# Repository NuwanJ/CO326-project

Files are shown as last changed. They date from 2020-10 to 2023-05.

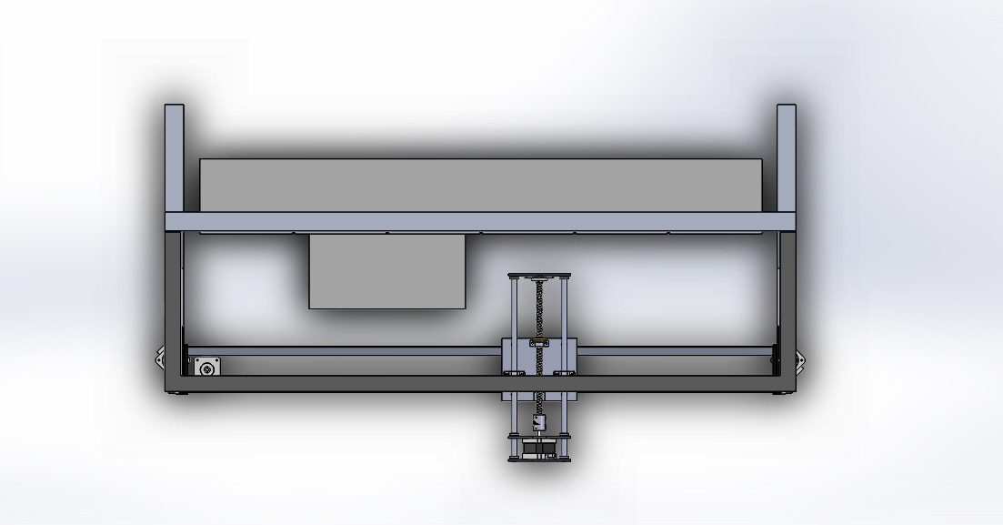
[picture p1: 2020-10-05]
views/top.JPG

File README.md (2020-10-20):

# CNC base 3-axis remotely controlled pick and place robot
### CO326 Computer Systems Engineering

## Overview
Overview
Over the past few decades technology has been evolving rapidly in so many aspects and fields to reach out to the human population in a more user-friendly manner. With these technological developments, new terms like “distance learning”, “remote laboratories”, “virtual learning environments” etc have emerged. However, labs have the greatest potential to overcome the bottleneck in distance education. The goal of Remote Laboratory implementation is to grant students access to laboratory equipment and cover physical laboratory exercises remotely.

A programmable logic controller (PLC) is a special purpose industrial computer/controller that has been adapted to control manufacturing processes. Hence, PLC is widely used in manufacturing to organize complex tasks like security monitoring, automatic control production lines, and management of energy consumption. As a result, there is a great need for engineers with knowledge of PLC. High cost, limited equipment, and limited access to this equipment make it difficult to access everyone.

Hence, connecting PLC with the remote laboratory enables educational institutions to offer programs to a much broader target group of potential students who under no circumstances are able to travel to and attend on-site sessions.

In this project, we hope to develop a CNC (Computer Numerical Control) based pick and place arm, which will help to try different wiring arrangements in a PLC rig and try experiments one it remotely.

Figure 1: An example of a Pick and Place CNC machine

Figure 2: PLC Test Rig of the department of computer engineering

## Specifications
### Software Layer
Web HMI with Javascript
MQTT broker for communication
### Hardware Software Interface
Using standard G-code language for machine control
A firmware like Merlin/Gerber will be supposed to use
Communication is done by USART protocol, with a baud rate of 115000bps
### Hardware Layer
- Nema17 standard stepper motors for motion control
- DRV8825 for stepper motor control
- Arduino Mega 2560 for motion planning

# Methodology

It is constructed using the CNC technology, using Stepper motors with a combination of Screw and Bolt mechanism (for Y and Z axises) and Belt and Pulley mechanism (For X axis). Stepper motors are driven by DRV8825 Step stick drivers with microstepping of 1/16 mode. The microcontroller for the machine is Arduino Mega 2560, with the support of RAMPS 1.4 shield for additional hardware.

The firmware we used is known as GRBL, a well known firmware which drives CNC machines using AVR family microcontrollers. We used GCODE to instruct the machine about movements in 3d space. The software named ‘Candle’ is used to control the machine from PC, and send machine commands as well as configuration commands.    

Communication protocol between HMI and the server needed careful consideration. The messages should be exchanged through the public internet and it should be lightweight since the messages need to arrive with minimum latency which could potentially disrupt the operation of the CNC machine. Therefore, the protocol should be able to handle unreliable networks. Also the messages only contain small commands that need to be passed to the hardware controller. Therefore, the message overhead should be minimum. And most importantly it should be able to handle multiple users. So students can work in groups controlling the PLC rig remotely. Considering all these requirements we used MQTT (Message Queue Telemetry Transport) as the message passing protocol. Because, MQTT is a lightweight message protocol that is based on a subscription-publishing model, in which publishers send messages to a server and this is who forwards messages to subscribers avoiding point-to-point connections between subscribers and publishers.

Students can log into the remote platform using the HMI developed using Javascript (along with HTML and CSS). Then they can use the HMI to send signals to control the CNC machine. The control messages get published to a MQTT broker. A server physically connected to the hardware controller subscribed to the MQTT broker receives the control messages. The control messages contain GCODE commands needed to control  the machine. The server sends the G-CODE commands through a serial interface to the ATMEGA 2560 which runs the GRBL. GRBL converts the control signals to electronic signals and sends to the motor driver, which controls the three server motors. This moves the 3-axis of the CNC machine.   

## Design





### Team Members
 - Jaliyagoda A.J.N.M. (E/15/140)
 - Karunarathna S.D.D.D. (E/15/173)
 - Tennakoon T.M.P.B. (E/15/350)

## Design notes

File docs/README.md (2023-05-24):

---
layout: home
permalink: index.html

# Please update this with your repository name and title
repository-name: e15-co326-remotely-controlled-cnc-robot
title: CNC base 3-axis remotely controlled pick and place robot
---

# CNC base 3-axis remotely controlled pick and place robot

---

## Team
- Jaliyagoda A.J.N.M. (E/15/140)
- Karunarathna S.D.D.D. (E/15/173)
- Tennakoon T.M.P.B. (E/15/350)

## Table of Contents
1. [Introduction](#introduction)
2. [Specifications](#specifications)
3. [Methodology](#methodology)
4. [Design](#design)
5. [Links](#links)

---

# Introduction
Over the past few decades technology has been evolving rapidly in so many aspects and fields to reach out to the human population in a more user-friendly manner. With these technological developments, new terms like “distance learning”, “remote laboratories”, “virtual learning environments” etc have emerged. However, labs have the greatest potential to overcome the bottleneck in distance education. The goal of Remote Laboratory implementation is to grant students access to laboratory equipment and cover physical laboratory exercises remotely.

A programmable logic controller (PLC) is a special purpose industrial computer/controller that has been adapted to control manufacturing processes. Hence, PLC is widely used in manufacturing to organize complex tasks like security monitoring, automatic control production lines, and management of energy consumption. As a result, there is a great need for engineers with knowledge of PLC. High cost, limited equipment, and limited access to this equipment make it difficult to access everyone.

Hence, connecting PLC with the remote laboratory enables educational institutions to offer programs to a much broader target group of potential students who under no circumstances are able to travel to and attend on-site sessions.

In this project, we hope to develop a CNC (Computer Numerical Control) based pick and place arm, which will help to try different wiring arrangements in a PLC rig and try experiments one it remotely.

Figure 1: An example of a Pick and Place CNC machine

Figure 2: PLC Test Rig of the department of computer engineering

## Specifications

### Software Layer
Web HMI with Javascript
MQTT broker for communication

### Hardware Software Interface
Using standard G-code language for machine control
A firmware like Merlin/Gerber will be supposed to use
Communication is done by USART protocol, with a baud rate of 115000bps

### Hardware Layer
- Nema17 standard stepper motors for motion control
- DRV8825 for stepper motor control
- Arduino Mega 2560 for motion planning

# Methodology

It is constructed using the CNC technology, using Stepper motors with a combination of Screw and Bolt mechanism (for Y and Z axises) and Belt and Pulley mechanism (For X axis). Stepper motors are driven by DRV8825 Step stick drivers with microstepping of 1/16 mode. The microcontroller for the machine is Arduino Mega 2560, with the support of RAMPS 1.4 shield for additional hardware.

The firmware we used is known as GRBL, a well known firmware which drives CNC machines using AVR family microcontrollers. We used GCODE to instruct the machine about movements in 3d space. The software named ‘Candle’ is used to control the machine from PC, and send machine commands as well as configuration commands.    

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

Students can log into the remote platform using the HMI developed using JavaScript (along with HTML and CSS). Then they can use the HMI to send signals to control the CNC machine. The control messages get published to a MQTT broker. A server physically connected to the hardware controller subscribed to the MQTT broker receives the control messages. The control messages contain GCODE commands needed to control  the machine. The server sends the G-CODE commands through a serial interface to the ATMEGA 2560 which runs the GRBL. GRBL converts the control signals to electronic signals and sends to the motor driver, which controls the three server motors. This moves the 3-axis of the CNC machine.   

## Design





## Funding

This project was funded by the *Prof. Suhada Jayasuriya Project Support Fund* through *PEFAA* [https://pefaa.net/](https://pefaa.net/).
PEFAA

## Links

- [Project Repository](https://github.com/cepdnaclk/{{ page.repository-name }}){:target="_blank"}
- [Project Page](https://cepdnaclk.github.io/{{ page.repository-name}}){:target="_blank"}
- [Department of Computer Engineering](http://www.ce.pdn.ac.lk/)
- [University of Peradeniya](https://eng.pdn.ac.lk/)

[//]: # (Please refer this to learn more about Markdown syntax)
[//]: # (https://github.com/adam-p/markdown-here/wiki/Markdown-Cheatsheet)

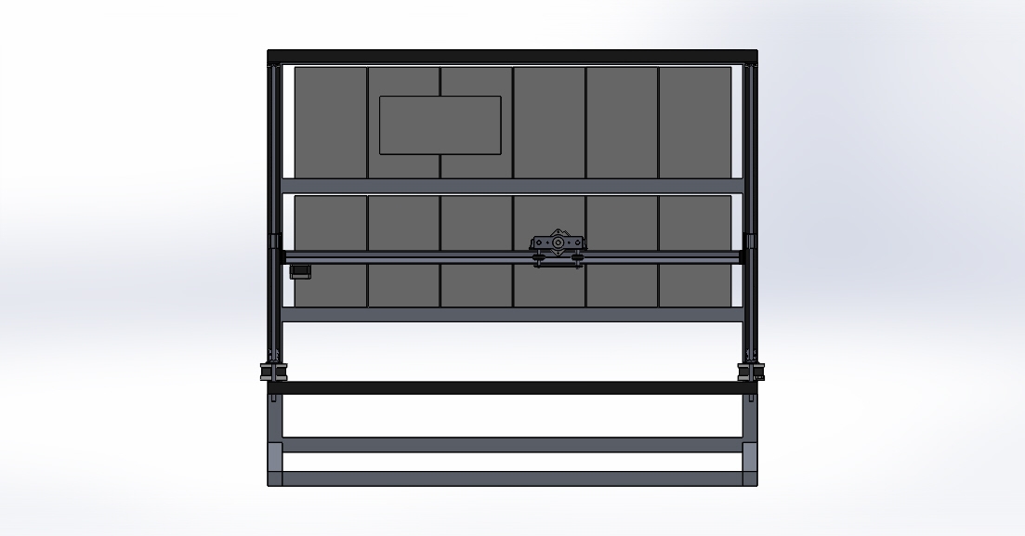
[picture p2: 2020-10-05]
views/front.JPG

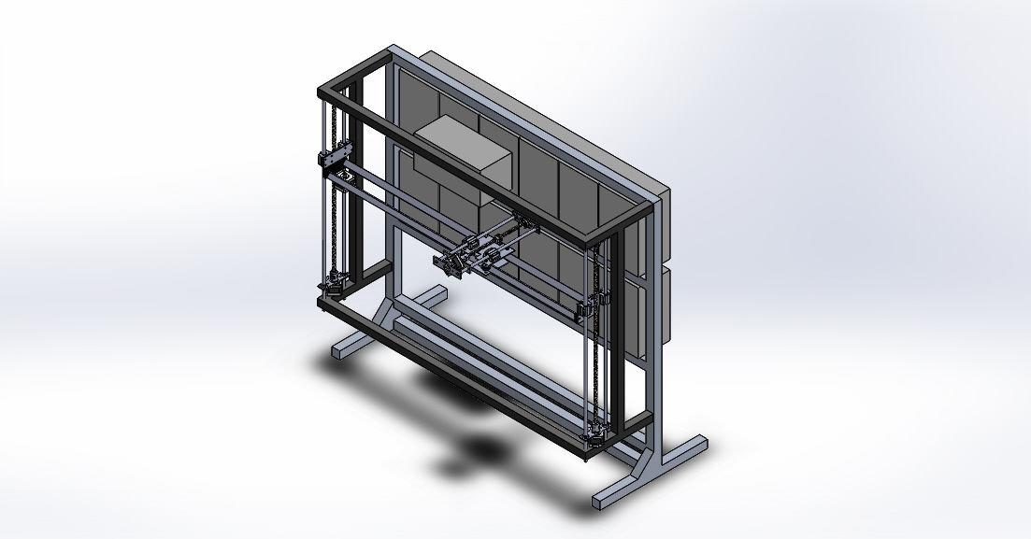
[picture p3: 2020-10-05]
views/orthogonal.JPG

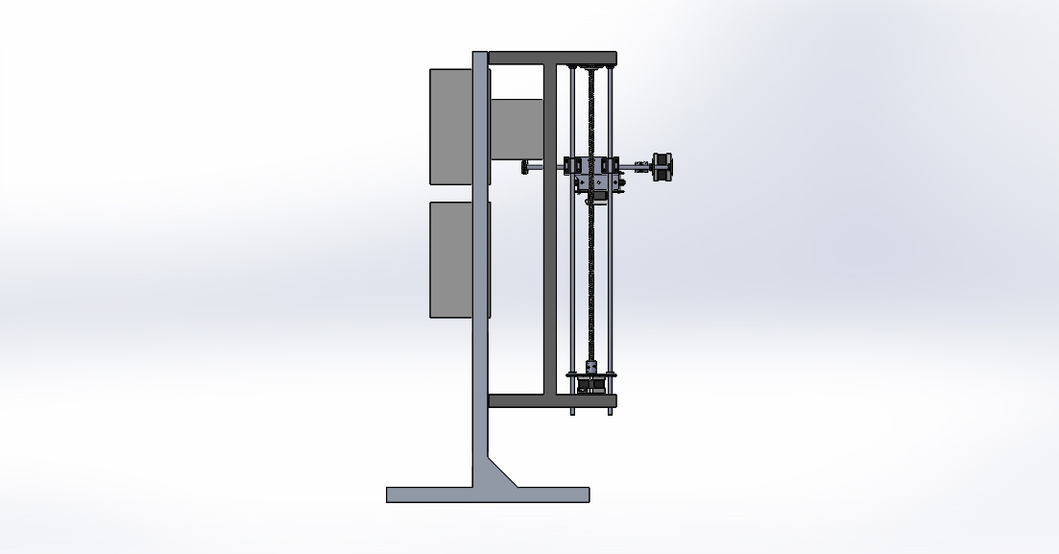
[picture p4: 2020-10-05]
views/side.JPG

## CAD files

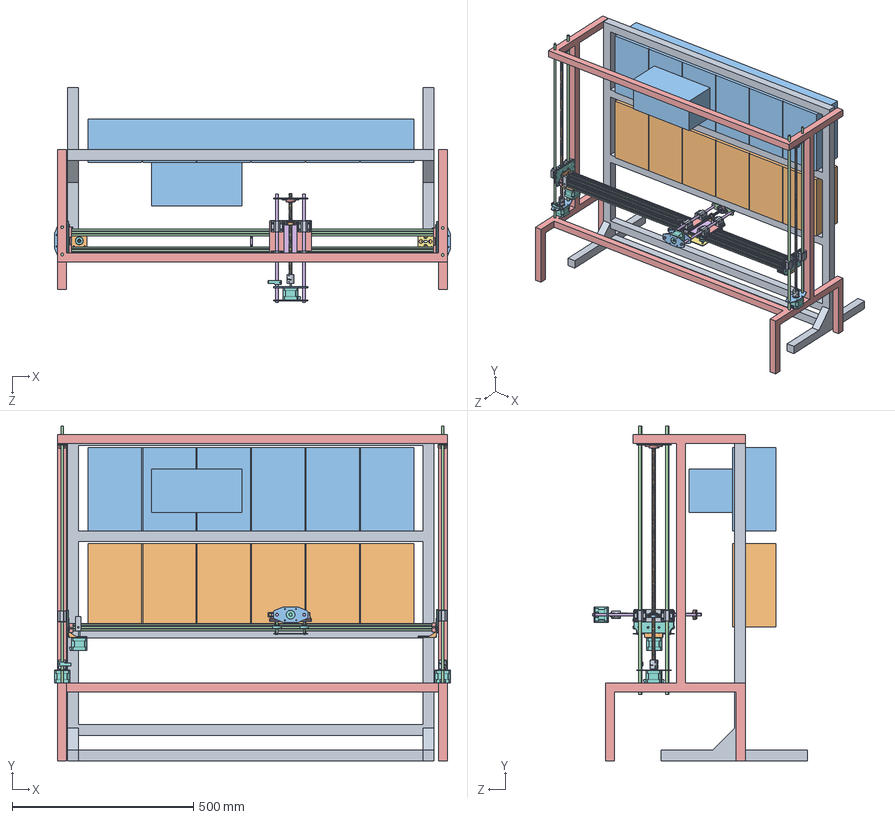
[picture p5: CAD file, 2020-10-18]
CAD/assembly.SLDASM
1092.1 x 923.0 x 593.6 mm
base_frame
components_lower
components_upper
8x600_SmoothRod x 4
kf8_kf08KFL08 x 3
kf8_kf08608RS x 3
kf8_kf08MOSCAM2,5 x 6
nema-17 x 4
5x8_shaft_coupling x 3
Trapezoidal lead screw tr8x8-4 x 2
axis_bracketA x 5
axis_bracketB x 3
metal_frame
x_bearing_bracket_top x 2
x_bearing_bracket_bottom
pom_wheel x 4
SC8UU x 8
T8_bracket
t8-nut x 3
M8x40 x 4
z_bearing_spacer x 4
z_smooth_rod x 2
z_lead_screw
y_bearing_bracket x 4
y_bearing_bracket_b x 2
Nema17_bracket x 2
T8_bracket_b x 2
2020_V-Slot x 2
2020_holder x 2
2020_spacer
pulley_idler_holder
y_limit_switch_holder x 2
x_limit_switch_holder

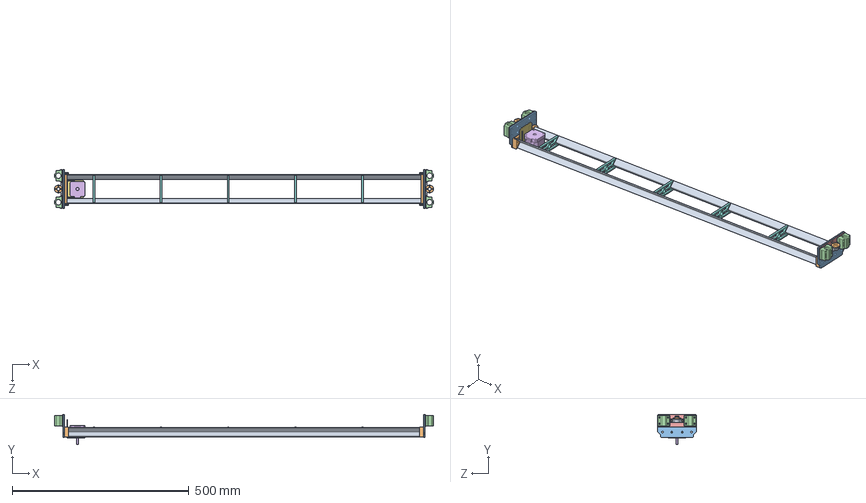
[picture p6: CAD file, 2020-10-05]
CAD/SubAssembly/x-assembly.SLDASM
1072.0 x 85.3 x 109.0 mm
x_rail x 2
x_rail_spacer_end x 2
y_bearing_bracket x 4
SC8UU x 4
y_bearing_bracket_b x 2
nema-17
Nema17_bracket
x_rail_spacer_mid x 5
T8_bracket_b x 2
t8-nut x 2

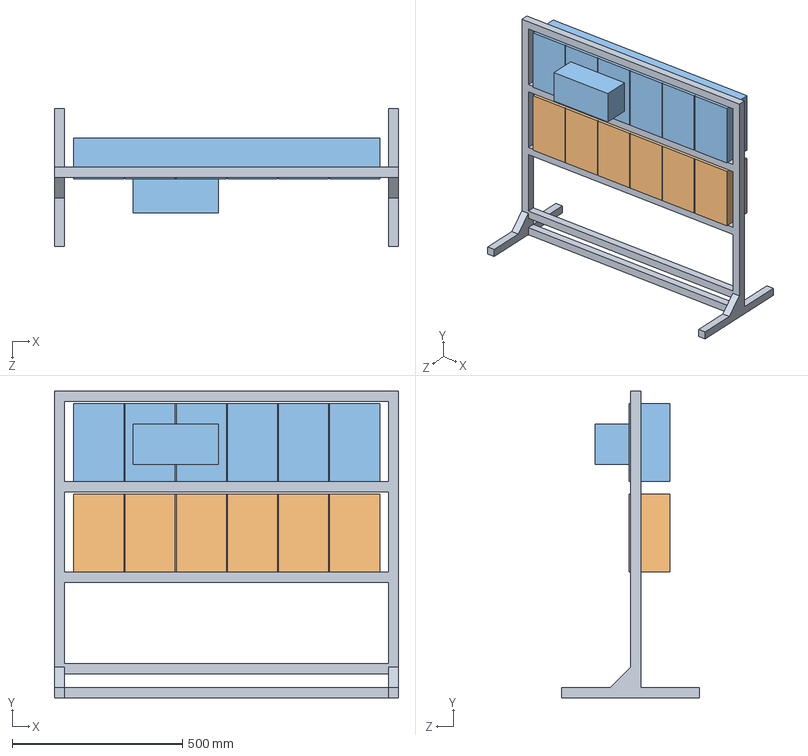
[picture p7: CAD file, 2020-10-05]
CAD/plc_rig.SLDASM
1010.0 x 900.0 x 405.0 mm
base_frame
components_lower
components_upper

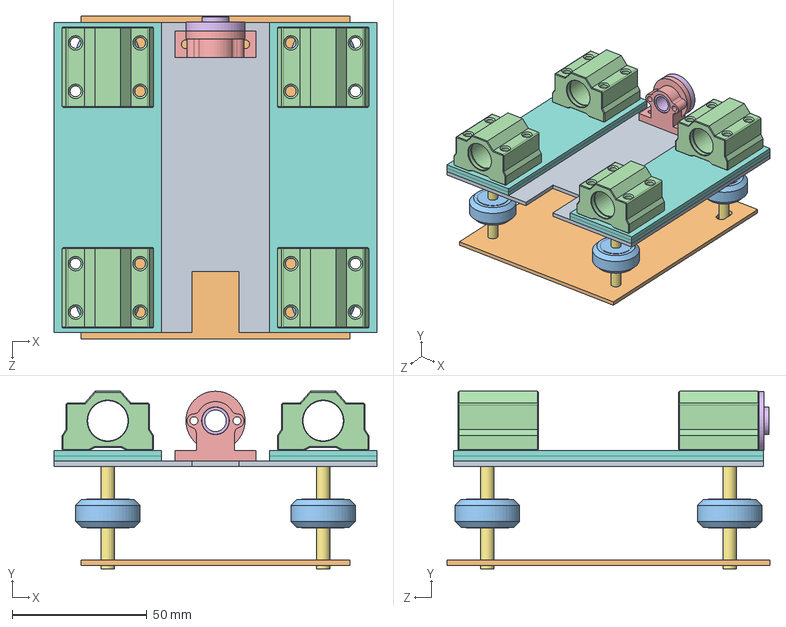
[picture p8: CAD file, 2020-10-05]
CAD/SubAssembly/z-assembly.SLDASM
120.0 x 66.0 x 120.0 mm
x_bearing_bracket_top
x_bearing_bracket_bottom
pom_wheel x 4
SC8UU x 4
T8_bracket
t8-nut
M8x40 x 4
z_bearing_spacer x 4

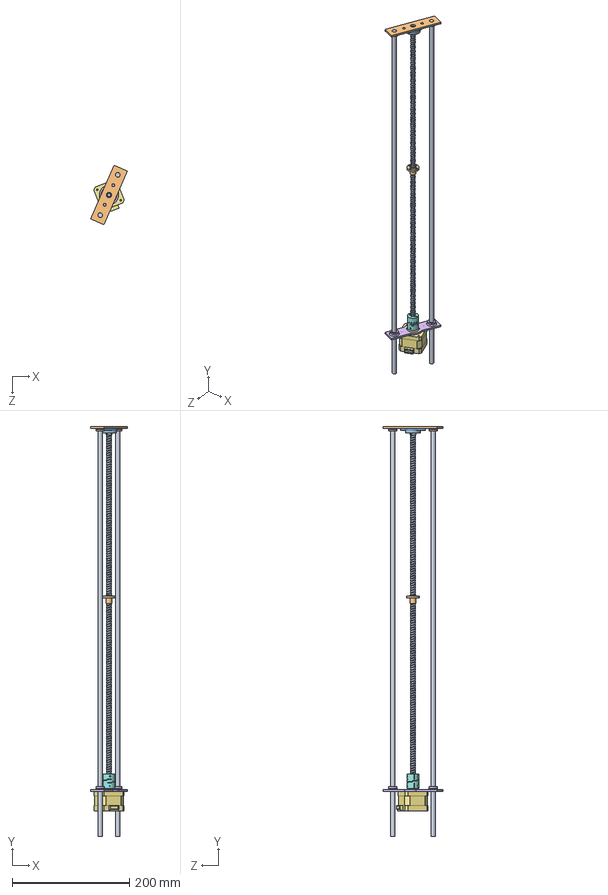
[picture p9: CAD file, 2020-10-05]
CAD/SubAssembly/y-assembly.SLDASM
63.0 x 700.0 x 101.6 mm
8x600_SmoothRod x 2
Y_linear_bracket
kf8_kf08KFL08
kf8_kf08608RS
kf8_kf08MOSCAM2,5 x 2
Y_linear_bracket_withMotor
nema-17
5x8_shaft_coupling
Trapezoidal lead screw tr8x8-4
t8-nut

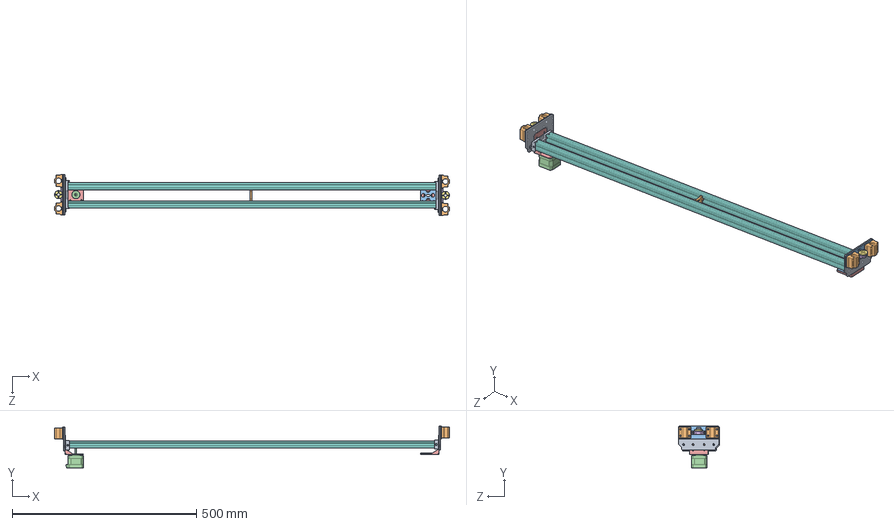
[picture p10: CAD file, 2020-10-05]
CAD/SubAssembly/x-assembly_v2.SLDASM
1071.5 x 113.4 x 110.8 mm
y_bearing_bracket x 4
SC8UU x 4
y_bearing_bracket_b x 2
nema-17
Nema17_bracket x 2
T8_bracket_b x 2
t8-nut x 2
2020_V-Slot x 2
2020_holder x 2
2020_spacer
pulley_idler_holder

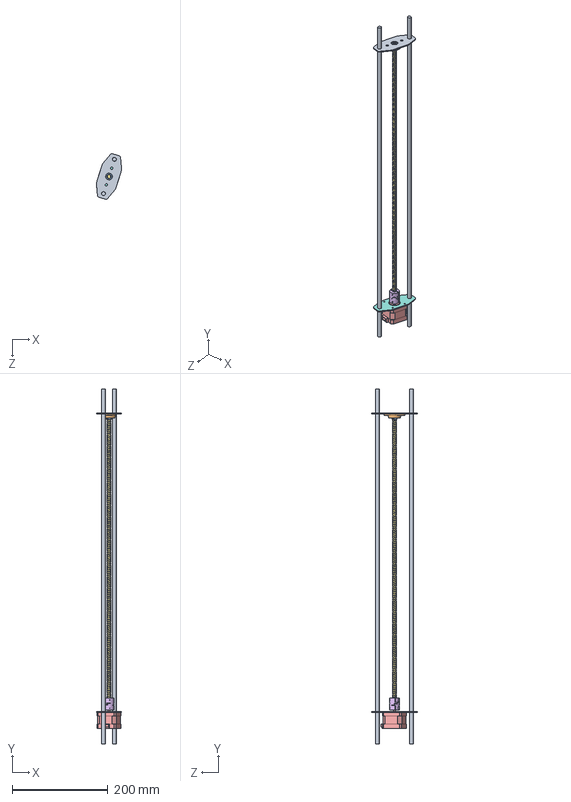
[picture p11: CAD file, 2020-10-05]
CAD/y-assembly.SLDASM
52.8 x 740.0 x 95.3 mm
8x600_SmoothRod x 2
kf8_kf08KFL08
kf8_kf08608RS
kf8_kf08MOSCAM2,5 x 2
nema-17
5x8_shaft_coupling
Trapezoidal lead screw tr8x8-4
axis_bracketA
axis_bracketB

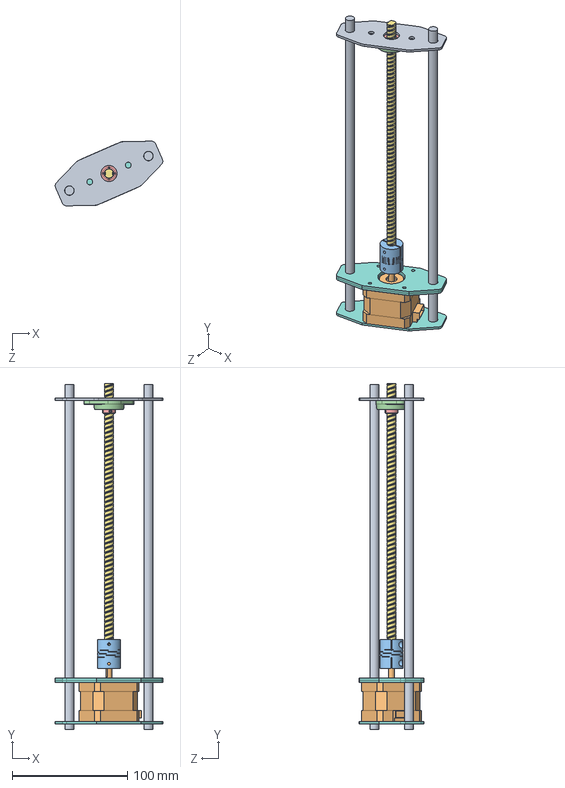
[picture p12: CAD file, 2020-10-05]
CAD/SubAssembly/z-moving-arm.SLDASM
93.6 x 300.7 x 56.3 mm
z_smooth_rod x 2
nema-17
5x8_shaft_coupling
kf8_kf08KFL08
kf8_kf08608RS
kf8_kf08MOSCAM2,5 x 2
z_lead_screw
axis_bracketA x 3
axis_bracketB

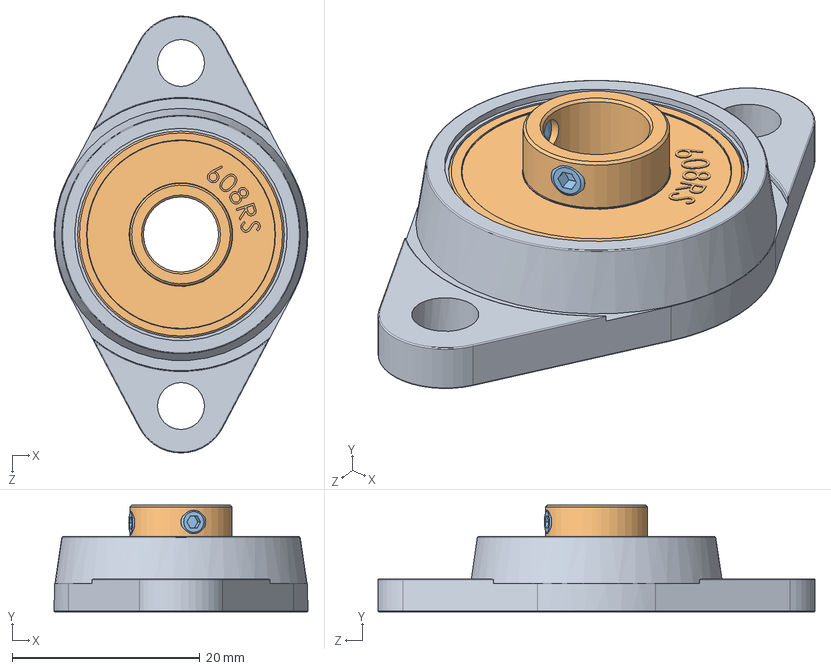
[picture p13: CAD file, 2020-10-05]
CAD/StdParts/KFL08.SLDASM
27.0 x 11.4 x 46.5 mm
kf8_kf08KFL08
kf8_kf08608RS
kf8_kf08MOSCAM2,5 x 2

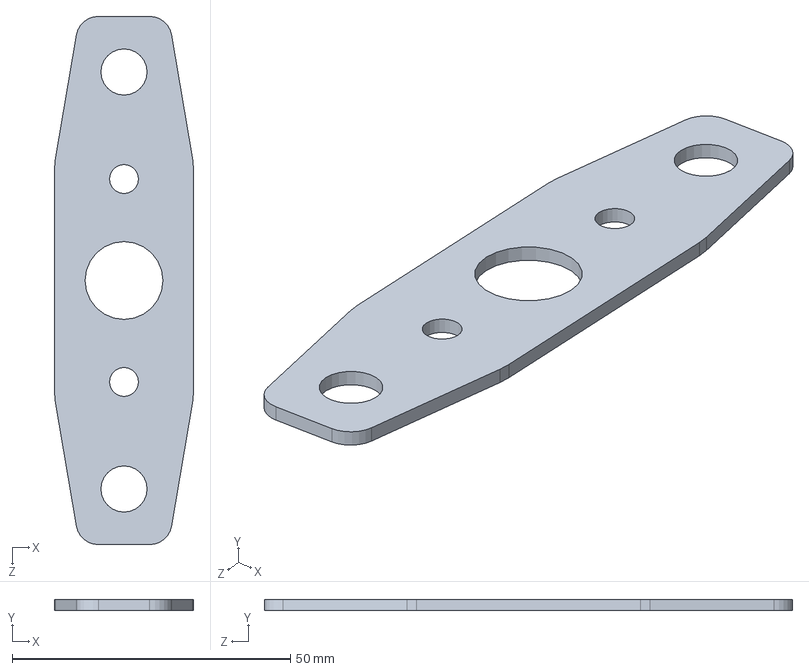
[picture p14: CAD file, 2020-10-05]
CAD/Parts/axis_bracketB.SLDPRT
25.0 x 2.00 x 95.0 mm

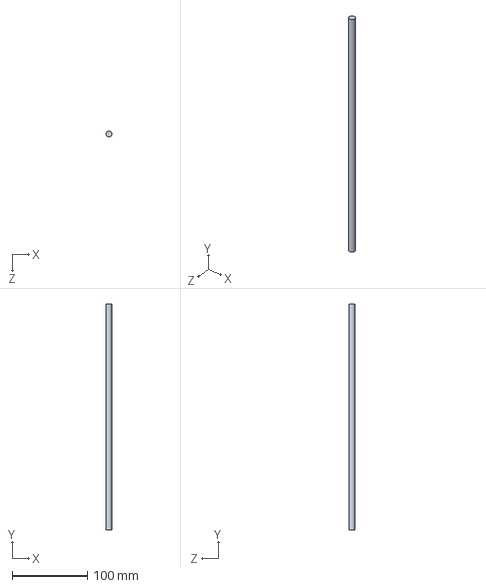
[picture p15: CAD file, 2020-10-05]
CAD/StdParts/z_smooth_rod.SLDPRT
8.00 x 300.0 x 8.00 mm

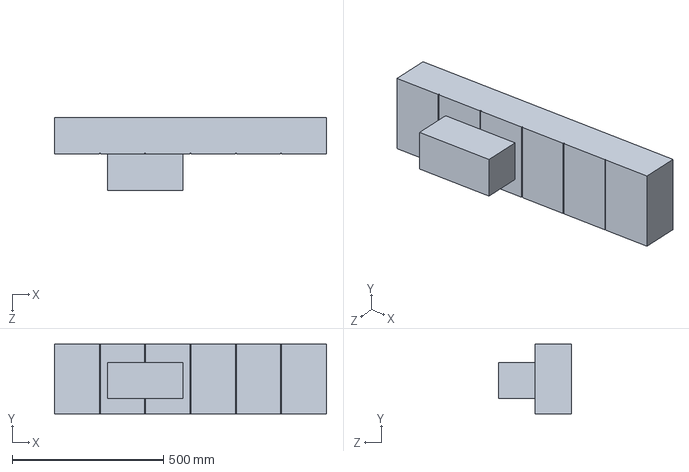
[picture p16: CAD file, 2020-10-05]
CAD/Parts/components_upper.SLDPRT
900.0 x 230.0 x 240.0 mm

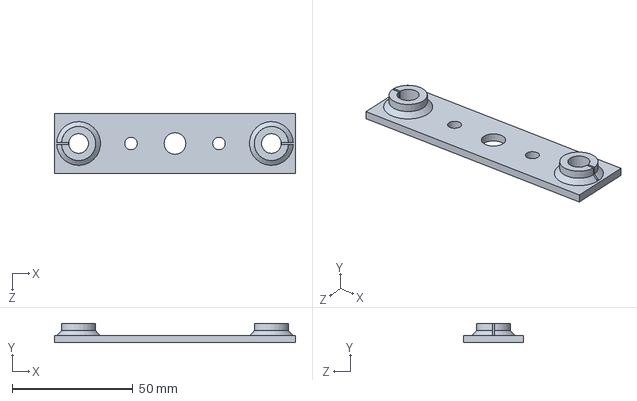
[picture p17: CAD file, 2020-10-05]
CAD/Parts/z_linear_bracket.SLDPRT
100.0 x 8.00 x 25.0 mm

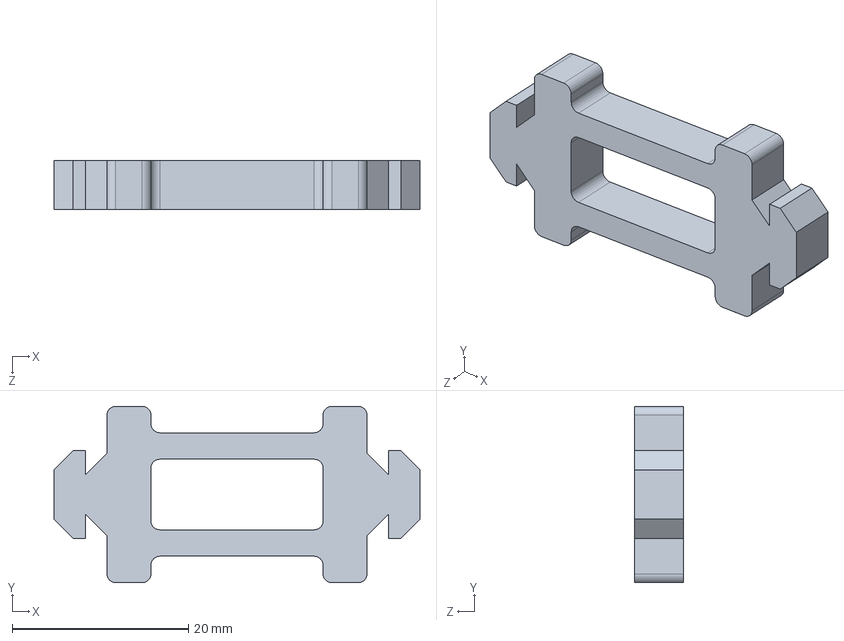
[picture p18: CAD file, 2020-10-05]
CAD/StdParts/2020_spacer.SLDPRT
41.5 x 20.0 x 5.50 mm

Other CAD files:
CAM/3d_prints/x_rail_spacer_mid.STL
CAM/3d_prints/x_rail_spacer_end.STL
CAM/3d_prints/y_spacer.STL
CAD/Parts/T8_bracket.SLDPRT
CAD/Parts/T8_bracket_b.SLDPRT
CAD/Parts/T8_holder.SLDPRT
CAD/Parts/Y_linear_bracket.SLDPRT
CAD/Parts/Y_linear_bracket_withMotor.SLDPRT
CAD/Parts/axis_bracketA.SLDPRT
CAD/Parts/base_frame.SLDPRT
CAD/Parts/bolt_spacer.SLDPRT
CAD/Parts/components_lower.SLDPRT
CAD/Parts/metal_frame.SLDPRT
CAD/Parts/pulley_idler_holder.SLDPRT
CAD/Parts/x_bearing_bracket_bottom.SLDPRT
CAD/Parts/x_bearing_bracket_top.SLDPRT
CAD/Parts/x_limit_switch_holder.SLDPRT
CAD/Parts/x_rail.SLDPRT
CAD/Parts/x_rail_spacer.SLDPRT
CAD/Parts/x_rail_spacer_end.SLDPRT
CAD/Parts/x_rail_spacer_mid.SLDPRT
CAD/Parts/y_bearing_bracket.SLDPRT
CAD/Parts/y_bearing_bracket_b.SLDPRT
CAD/Parts/y_limit_switch_holder.SLDPRT
CAD/Parts/y_spacer.SLDPRT
CAD/Parts/z_bearing_spacer.SLDPRT
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

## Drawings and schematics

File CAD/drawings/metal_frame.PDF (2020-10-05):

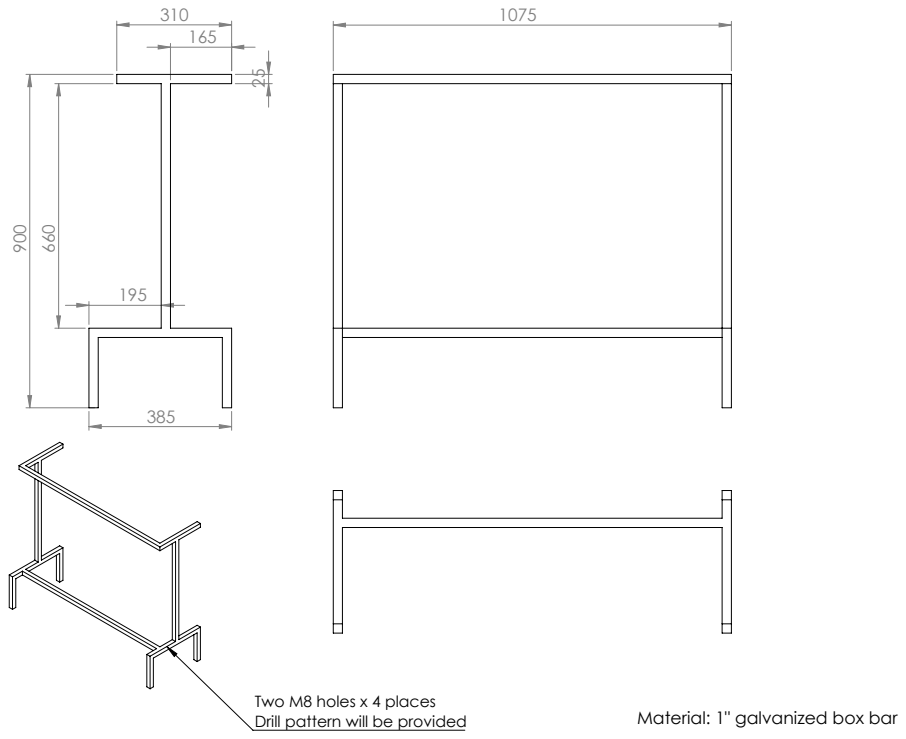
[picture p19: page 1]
Drill pattern will be provided; Material: 1" galvanized box bar

Two M8 holes x 4 places

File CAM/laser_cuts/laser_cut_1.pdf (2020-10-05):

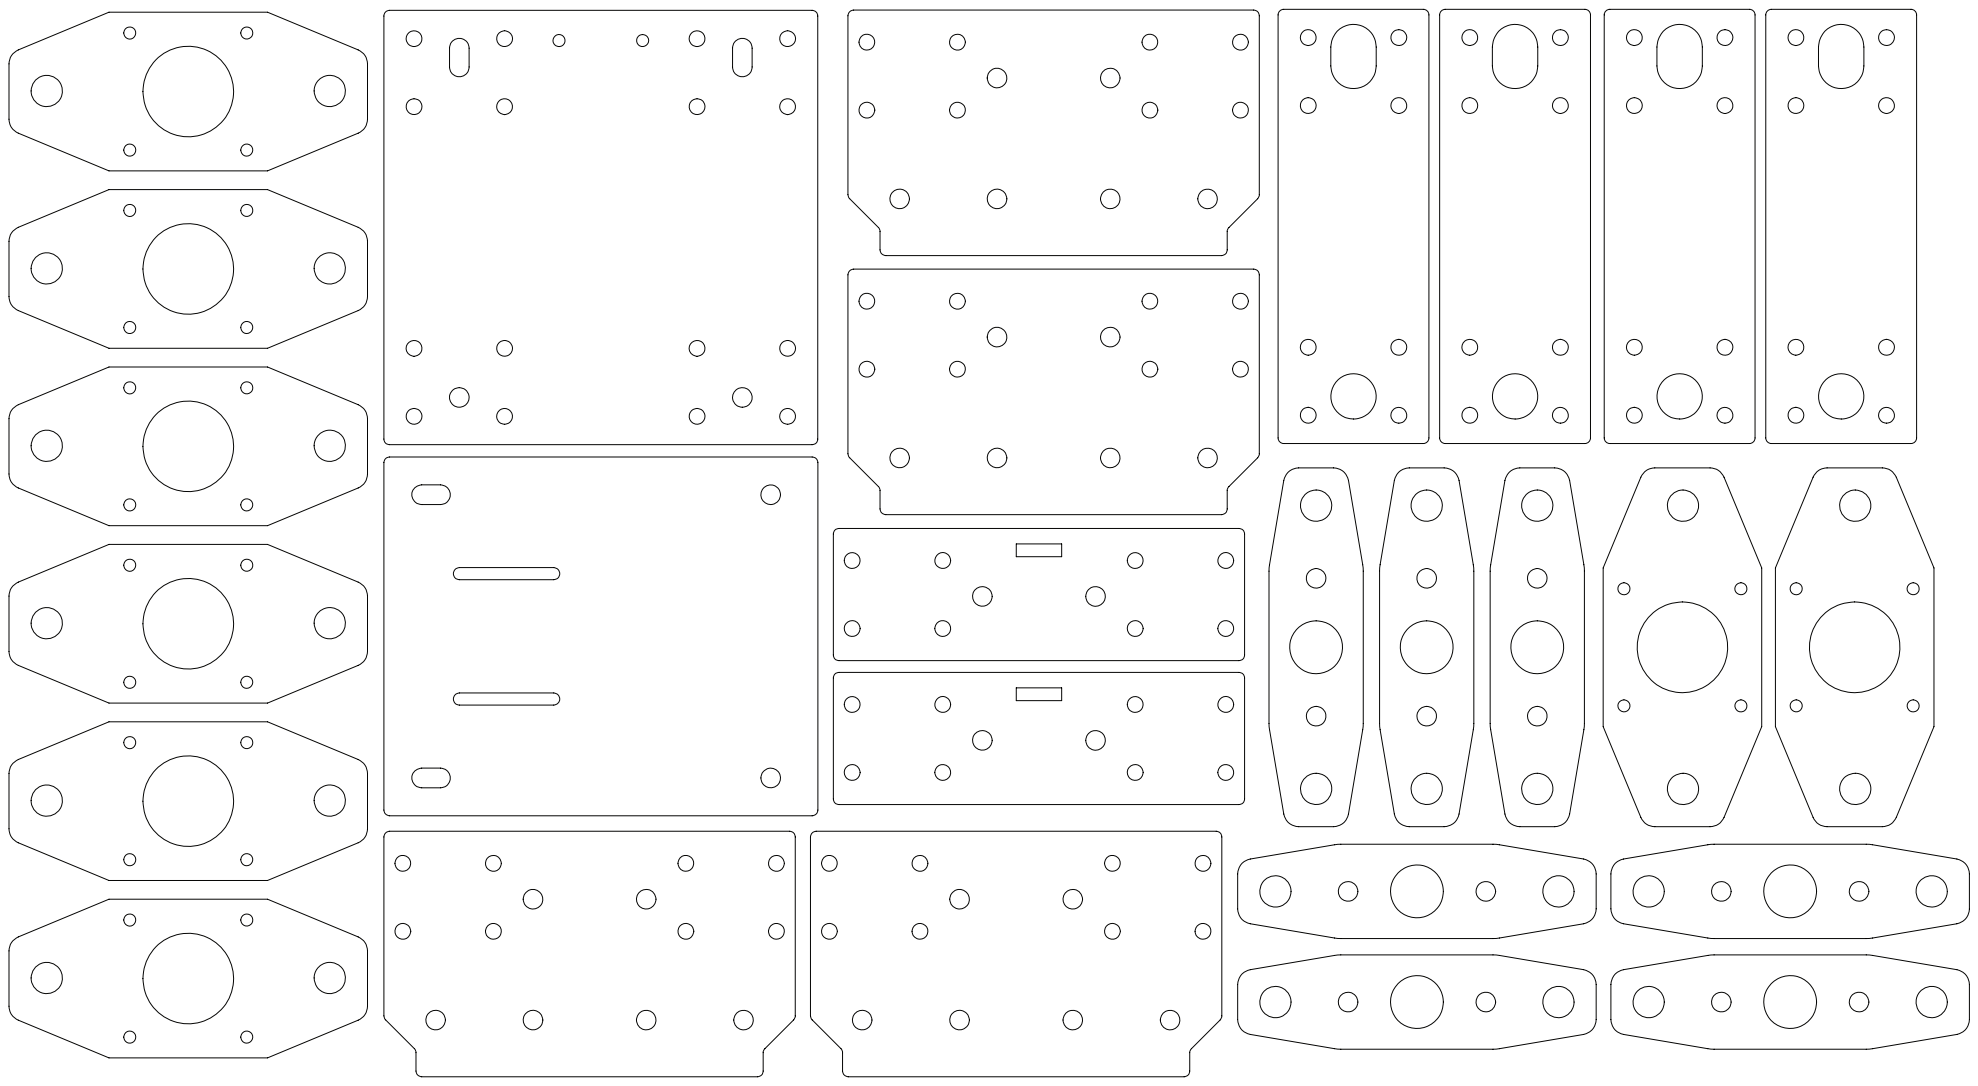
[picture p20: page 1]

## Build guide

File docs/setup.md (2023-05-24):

## Install Node JS (linux)

```
sudo apt-get update
sudo apt install nodejs
```
## Install Node JS (windows)

Follow this tutorial:
[install-node-js-npm-on-windows](https://phoenixnap.com/kb/install-node-js-npm-on-windows)

## Setup the software

1. Download the program using this link: 
[cepdnaclk.github.io/e15-co326-remotely-controlled-cnc-robot/nodeServer.zip](https://cepdnaclk.github.io/e15-co326-remotely-controlled-cnc-robot/nodeServer.zip)

2. Extract the content on the zip and open the terimnal insite the program. 

3. Next type the following instructionss on terminal for complete the installation.

```
npm install
```

## Run the software (windows)

1. Connect the machine into PC
2. Identify the COM port number, using device manager or any other application
3. Run the following command. (Change the port COMX with the port number you obtained in step 2)

```
npm start COMX
```

## View controller software

You can view it from  [https://cepdnaclk.github.io/e15-co326-remotely-controlled-cnc-robot/web/](https://cepdnaclk.github.io/e15-co326-remotely-controlled-cnc-robot/web/)

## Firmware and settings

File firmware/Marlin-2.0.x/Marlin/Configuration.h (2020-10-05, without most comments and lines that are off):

#pragma once
#define CONFIGURATION_H_VERSION 020000
#define STRING_CONFIG_H_AUTHOR "(none, default config)" // Who made the changes.
#define SHOW_BOOTSCREEN
#define SERIAL_PORT 0
#define BAUDRATE 115200
  #define MOTHERBOARD BOARD_RAMPS_14_EFB
#define EXTRUDERS 1
#define DEFAULT_NOMINAL_FILAMENT_DIA 3.0
#define TEMP_SENSOR_0 1
#define TEMP_SENSOR_1 0
#define TEMP_SENSOR_2 0
#define TEMP_SENSOR_3 0
#define TEMP_SENSOR_4 0
#define TEMP_SENSOR_5 0
#define TEMP_SENSOR_6 0
#define TEMP_SENSOR_7 0
#define TEMP_SENSOR_BED 0
#define TEMP_SENSOR_PROBE 0
#define TEMP_SENSOR_CHAMBER 0
#define DUMMY_THERMISTOR_998_VALUE 25
#define DUMMY_THERMISTOR_999_VALUE 100
#define MAX_REDUNDANT_TEMP_SENSOR_DIFF 10
#define TEMP_RESIDENCY_TIME     10  // (seconds) Time to wait for hotend to "settle" in M109
#define TEMP_WINDOW              1  // (°C) Temperature proximity for the "temperature reached" timer
#define TEMP_HYSTERESIS          3  // (°C) Temperature proximity considered "close enough" to the target
#define TEMP_BED_RESIDENCY_TIME 10  // (seconds) Time to wait for bed to "settle" in M190
#define TEMP_BED_WINDOW          1  // (°C) Temperature proximity for the "temperature reached" timer
#define TEMP_BED_HYSTERESIS      3  // (°C) Temperature proximity considered "close enough" to the target
#define HEATER_0_MINTEMP   5
#define HEATER_1_MINTEMP   5
#define HEATER_2_MINTEMP   5
#define HEATER_3_MINTEMP   5
#define HEATER_4_MINTEMP   5
#define HEATER_5_MINTEMP   5
#define HEATER_6_MINTEMP   5
#define HEATER_7_MINTEMP   5
#define BED_MINTEMP        5
#define HEATER_0_MAXTEMP 275
#define HEATER_1_MAXTEMP 275
#define HEATER_2_MAXTEMP 275
#define HEATER_3_MAXTEMP 275
#define HEATER_4_MAXTEMP 275
#define HEATER_5_MAXTEMP 275
#define HEATER_6_MAXTEMP 275
#define HEATER_7_MAXTEMP 275
#define BED_MAXTEMP      150
#define PIDTEMP
#define BANG_MAX 255     // Limits current to nozzle while in bang-bang mode; 255=full current
#define PID_MAX BANG_MAX // Limits current to nozzle while PID is active (see PID_FUNCTIONAL_RANGE below); 255=full current
#define PID_K1 0.95      // Smoothing factor within any PID loop
  #define PID_FUNCTIONAL_RANGE 10 // If the temperature difference between the target temperature and the actual temperature
  #define DEFAULT_Kp 22.2
  #define DEFAULT_Ki 1.08
  #define DEFAULT_Kd 114
#define MAX_BED_POWER 255 // limits duty cycle to bed; 255=full current
#define PREVENT_COLD_EXTRUSION
#define EXTRUDE_MINTEMP 170
#define PREVENT_LENGTHY_EXTRUDE
#define EXTRUDE_MAXLENGTH 200
#define THERMAL_PROTECTION_HOTENDS // Enable thermal protection for all extruders
#define THERMAL_PROTECTION_BED     // Enable thermal protection for the heated bed
#define THERMAL_PROTECTION_CHAMBER // Enable thermal protection for the heated chamber
#define USE_XMIN_PLUG
#define USE_YMIN_PLUG
#define USE_ZMAX_PLUG
#define ENDSTOPPULLUPS
#define X_MIN_ENDSTOP_INVERTING true // Set to true to invert the logic of the endstop.
#define Y_MIN_ENDSTOP_INVERTING true // Set to true to invert the logic of the endstop.
#define Z_MIN_ENDSTOP_INVERTING true // Set to true to invert the logic of the endstop.
#define X_MAX_ENDSTOP_INVERTING false // Set to true to invert the logic of the endstop.
#define Y_MAX_ENDSTOP_INVERTING false // Set to true to invert the logic of the endstop.
#define Z_MAX_ENDSTOP_INVERTING true // Set to true to invert the logic of the endstop.
#define Z_MIN_PROBE_ENDSTOP_INVERTING false // Set to true to invert the logic of the probe.
#define X_DRIVER_TYPE  DRV8825
#define Y_DRIVER_TYPE  DRV8825
#define Z_DRIVER_TYPE  DRV8825
#define DEFAULT_AXIS_STEPS_PER_UNIT   {200, 800, 800, 500 }
#define DEFAULT_MAX_FEEDRATE          { 600, 300, 50, 25 }
#define DEFAULT_MAX_ACCELERATION      { 500, 100, 100, 10000 }
#define DEFAULT_ACCELERATION          500    // X, Y, Z and E acceleration for printing moves
#define DEFAULT_RETRACT_ACCELERATION  3000    // E acceleration for retracts
#define DEFAULT_TRAVEL_ACCELERATION   500    // X, Y, Z acceleration for travel (non printing) moves
#define DEFAULT_EJERK    5.0  // May be used by Linear Advance
  #define JUNCTION_DEVIATION_MM 0.013 // (mm) Distance from real junction edge
#define NOZZLE_TO_PROBE_OFFSET { 10, 10, 0 }
#define MIN_PROBE_EDGE 10
#define XY_PROBE_SPEED 500
#define Z_PROBE_SPEED_FAST HOMING_FEEDRATE_Z
#define Z_PROBE_SPEED_SLOW (Z_PROBE_SPEED_FAST / 2)
#define Z_CLEARANCE_DEPLOY_PROBE   10 // Z Clearance for Deploy/Stow
#define Z_CLEARANCE_BETWEEN_PROBES  5 // Z Clearance between probe points
#define Z_CLEARANCE_MULTI_PROBE     5 // Z Clearance between multiple probes
#define Z_PROBE_LOW_POINT          -2 // Farthest distance below the trigger-point to go before stopping
#define Z_PROBE_OFFSET_RANGE_MIN -20
#define Z_PROBE_OFFSET_RANGE_MAX 20
#define X_ENABLE_ON 0
#define Y_ENABLE_ON 0
#define Z_ENABLE_ON 0
#define E_ENABLE_ON 0 // For all extruders
#define DISABLE_X true
#define DISABLE_Y true
#define DISABLE_Z true
#define DISABLE_E false             // For all extruders
#define DISABLE_INACTIVE_EXTRUDER   // Keep only the active extruder enabled
#define INVERT_X_DIR false
#define INVERT_Y_DIR true
#define INVERT_Z_DIR false
#define INVERT_E0_DIR false
#define INVERT_E1_DIR false
#define INVERT_E2_DIR false
#define INVERT_E3_DIR false
#define INVERT_E4_DIR false
#define INVERT_E5_DIR false
#define INVERT_E6_DIR false
#define INVERT_E7_DIR false
#define X_HOME_DIR -1
#define Y_HOME_DIR -1
#define Z_HOME_DIR 1
#define X_BED_SIZE 800
#define Y_BED_SIZE 500
#define X_MIN_POS 0
#define Y_MIN_POS 0
#define Z_MIN_POS 0
#define X_MAX_POS X_BED_SIZE
#define Y_MAX_POS Y_BED_SIZE
#define Z_MAX_POS 180
#define MIN_SOFTWARE_ENDSTOPS
  #define MIN_SOFTWARE_ENDSTOP_X
  #define MIN_SOFTWARE_ENDSTOP_Y
  #define MIN_SOFTWARE_ENDSTOP_Z
#define MAX_SOFTWARE_ENDSTOPS
  #define MAX_SOFTWARE_ENDSTOP_X
  #define MAX_SOFTWARE_ENDSTOP_Y
  #define MAX_SOFTWARE_ENDSTOP_Z
#define HOMING_FEEDRATE_XY 500 // (50*60)
#define HOMING_FEEDRATE_Z  500 // (10*60)
#define VALIDATE_HOMING_ENDSTOPS
#define EEPROM_CHITCHAT       // Give feedback on EEPROM commands. Disable to save PROGMEM.
#define HOST_KEEPALIVE_FEATURE        // Disable this if your host doesn't like keepalive messages
#define DEFAULT_KEEPALIVE_INTERVAL 2  // Number of seconds between "busy" messages. Set with M113.
#define BUSY_WHILE_HEATING            // Some hosts require "busy" messages even during heating
#define PREHEAT_1_LABEL       "PLA"
#define PREHEAT_1_TEMP_HOTEND 180
#define PREHEAT_1_TEMP_BED     70
#define PREHEAT_1_FAN_SPEED     0 // Value from 0 to 255
#define PREHEAT_2_LABEL       "ABS"
#define PREHEAT_2_TEMP_HOTEND 240
#define PREHEAT_2_TEMP_BED    110
#define PREHEAT_2_FAN_SPEED     0 // Value from 0 to 255
#define PRINTJOB_TIMER_AUTOSTART
#define LCD_LANGUAGE en
#define DISPLAY_CHARSET_HD44780 JAPANESE
#define LCD_INFO_SCREEN_STYLE 0
#define SOFT_PWM_SCALE 0
#define SERVO_DELAY { 300 }

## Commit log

2020-10-05 initial upload
    [2020_V-Slot.SLDPRT, 2020_holder.SLDPRT, 2020_holder.STL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]
2020-10-05 go to coordinate sample is working now
2020-10-06 sample drawings
2020-10-20 landing page
2021-06-26 Added LTS files
    [2020_holder.STL, 2020_spacer.STL, T8_bracket.STL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]

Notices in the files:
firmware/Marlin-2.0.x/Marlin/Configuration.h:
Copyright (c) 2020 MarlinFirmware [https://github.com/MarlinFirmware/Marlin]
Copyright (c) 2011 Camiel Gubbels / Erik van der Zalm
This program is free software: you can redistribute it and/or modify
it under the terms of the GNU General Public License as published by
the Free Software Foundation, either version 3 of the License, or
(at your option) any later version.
